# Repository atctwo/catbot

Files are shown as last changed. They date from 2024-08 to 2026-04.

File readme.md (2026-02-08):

# Cat Bot / Scratch
This repo contains the design files for **Cat Bot**, aka **Scratch**.  This is a 450g / 1lb class battlebot I made that looks like a cat.  It was designed for the [Robotics Society](https://linktr.ee/qub_robotics) at Queen's University Belfast (QRS), for competition at my local battlebots group [Combat Robotics NI](https://www.combatroboticsni.com/).

<center>
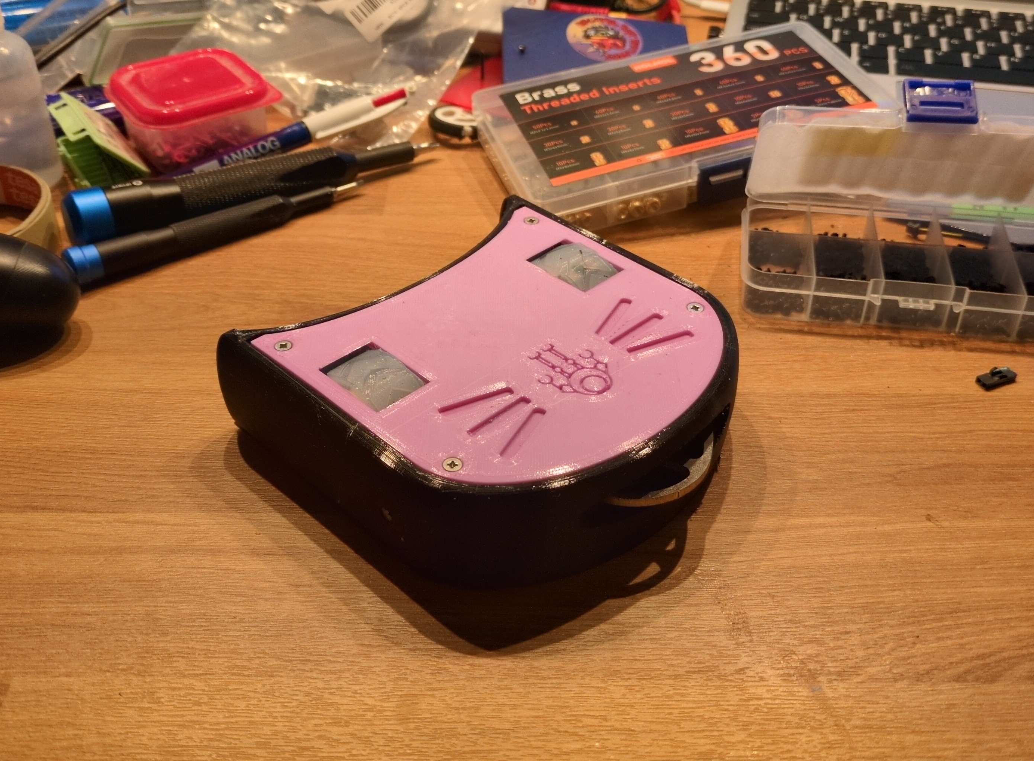
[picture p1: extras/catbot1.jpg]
A picture of Cat Bot sitting on a very messy wooden desk

</center>

# Features
- it looks like a cat :3
- (almost) the entire bot is printed from TPU to protect from impacts
- driven by two wheels (enclosed within the chassis for protection), which stick out the top and bottom to allow for operation when flipped
  - the QRS logo on the lids indicate the direction of "forward" for the motors, depending on which side is up
- multiple methods of offence
  - the cat's head is actually a plough which you can use to push opponents out of the arena
  - the cat's tongue is actually a spinner weapon so you can lick other opponents
  - you can decide which would be more useful based on your opponent
- internal walls to protect components from the wheels and the very fast spinner weapon
- designed using OpenSCAD, so *almost everything* is parametric and can be modified
- a [bill of materials](./docs/bom.md) and [build instructions](./docs/building.md) are provided to make replicating the bot easier
- external-facing screws are countersunk because it looks cool
- around 405 grams, and less than 140mm x 140mm x 40mm

# Building
A guide for building your own kitty friend are provided in [`docs/building.md`](./docs/building.md), along with the [bill of materials](./docs/bom.md)!

# Configurations
This bot was originally designed with two configurations: Little Cat and Big Cat.  As time went on, I only focused development on Little Cat so Big Cat kinda got left behind.  As such, it is deprecated and untested.  If you want to try Big Cat, check out git tag `v1.0.3`!

# Repo Structure
- [`exploded_view/`](./exploded_view/) - location to store images and render videos of an exploded view animation
- [`imports/`](./imports/) - external files imported by `cat_bot.scad` (eg: an SVG of the QRS logo)
- [`MCAD/`](./MCAD/) - submodule to [MCAD](https://github.com/openscad/MCAD), an OpenSCAD library dependency
- [`renders/`](./renders/) - exported STL versions of each part of each version of each configuration
- [`docs/`](./docs/) - documentation for the bot
  - [`building.md`](./docs/building.md) - cat bot build guide
  - [`bom.md`](./docs/bom.md) - bill of materials for each config
- [`src/`](./src/) - directory containing the OpenSCAD source code
  - [`cat_bot.scad`](./src/cat_bot.scad) - the main OpenSCAD source code file
  - [`cat_led_shim.scad`](./src/cat_led_shim.scad) - source code for the little shim that holds the power LED into the chassis
  - [`cat_wheel.scad`](./src/cat_wheel.scad) - source code for the custom wheels the bot uses
  - [`micro_metal_bracket.scad`](./src/micro_metal_bracket.scad) - a little bracket for the micro metal motors used by Little Cat
- [`readme.md`](./readme.md) - this readme!

# License
This is licensed under the MIT License - check out [`LICENSE`](./LICENSE) for more info.

# Acknowledgements
This has been one of the most interesting projects I've ever done.  I want to thank some of the people who helped me along the way!
- [Combat Robotics NI](https://www.combatroboticsni.com/) for providing a local space for destructive antweight battlebots, as well as the endless advice and assistance they've given me!
- [Team Penny](https://www.facebook.com/twopennymilk/) for their endless expertise and advice!

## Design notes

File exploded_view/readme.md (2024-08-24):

# Exploded View
This directory contains stuff to make an animated exploded view of the cat bot!

First, open `cat_bot.scad`.  Go to View -> Animate; this should open the animation bar below the 3D render pane.  Next, provide value for the FPS and Steps fields; normally I use 60 FPS and 240 steps.  Once you set these parameters the animation will start, and it will re-render the model for each step, so it can get quite laggy.  Once it's started, check the Dump Pictures box.  This will take a screenshot of each frame, and dump into the root of this repository's directory.  

After a few animation cycles and all the frames have been dumped, the Dump Pictures checkbox will uncheck itself.  Set the FPS to 0 and copy all the frame0000.png files into this directory.  To reset the model to it's unexploded state, reset the Time field to 0, then hide the animation bar.

> [!NOTE] Looping the animation
> The animation code is designed to make the animation loop automatically.  To achieve this, the model is at it's most exploded at time `$t=0.5`, and is not exploded at all at `$t=0` *and* `$t=1.0`.

Next, run [`make_exploded_view.sh`](./make_exploded_view.sh).  This will call `ffmpeg` and compile all the screenshots (specifically all .png files) into one mp4 file.  The rendered video is output as [`exploded_view.mp4`](./exploded_view.mp4):

<video controls src="exploded_view.mp4" title="Exploded View of Little Cat" loop></video>

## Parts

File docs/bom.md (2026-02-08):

# Bill Of Materials
This page lists all the parts needed to build a Cat Bot.  This is a list of all the stuff I used to build it, but a lot of it could easily be swapped out with other similar parts.  If you're using parts with different dimensions, it might be necessary to modify cat_bot.scad before printing.

Items in *italics* are need to be 3D printed.  Please refer to the [build guide](./building.md) for more detail on how to print the 3D printed parts.

| Item | Qty | Description and Notes | STL render |
|---|-----|---|---|
| **Main Chassis** | | | |
| *Chassis* | 1 | Ideally printed in TPU | [v1.3.2](../renders/little_cat/v1.3.2/main_chassis_v1.3.2a.stl) |
| *Top Lid (top)* | 1 | Ideally TPU, but PLA would probably work | [v1.3.2](../renders/little_cat/v1.3.2/top_lid_top_v1.3.2a.stl) |
| *Top Lid (bottom)* | 1 | Printed with PLA | [v1.3.2](../renders/little_cat/v1.3.2/top_lid_bottom_v1.3.2a.stl) |
| *Bottom Lid* | 1 | Ideally TPU, but PLA would probably work | [v1.3.2](../renders/little_cat/v1.3.2/bottom_lid_v1.3.2a.stl) |
| **Motors and Wheels** | | | |
| Micro Metal (N20) Gearbox Motor | 2 | 298:1 ratio is recommended | |
| *Micro Metal Bracket* | 2 | Printed with PLA or PETG | [v2](../renders/wheels/micro_metal_bracket_v2.stl) |
| Micro Metal Shim | 2 | Little shims made by [Pimoroni](https://shop.pimoroni.com/products/motor-shim-pack-of-5?variant=24169581255) so you don't have to solder directly to the motors | |
| Wheels | 2 | The bot is designed to use any 42mm diameter, 3mm shaft wheels.  However, this cat has custom wheels if you want to make them! |
| <em>&nbsp;&nbsp;&nbsp;&nbsp;Cat Wheel Hub</em> | 2 | Main hub of the wheels, printed in TPU | [v3](../renders/wheels/cat_wheel_v3.0_hub.stl) |
| <em>&nbsp;&nbsp;&nbsp;&nbsp;Cat Wheel Axel Insert</em> | 2 | 3mm shaft compatible insert, inserted into hub ([source](cat_wheel.scad), [STL](./renders/wheels/cat_wheel_v2_insert.stl)) | [v3](../renders/wheels/cat_wheel_v3.0_insert.stl) |
| <em>&nbsp;&nbsp;&nbsp;&nbsp;Cat Wheel Tyre</eM> | | Tyres for the wheels, cast out of silicone (again, pls refer to the build guide for more info!) | [v3](../renders/wheels/cat_wheel_v3.0_tyre.stl) |
| **Weapon** | | | |
| 60mm spinning blade | 1 | Currently using [this one](https://www.ull-robotics.com/shop/p/60mm-dia-disc) from ULL Robotics<br>Previously used [this one](https://monsoonrobotics.co.uk/collections/bars-and-discs) from Monsoon Robotics| |
| Brushless Motor | 1 | I'm currently using a BE1806 ([eg: this one from Bristol Bot Builders](https://shop.bristolbotbuilders.com/product/brushlessmotor/))| |
| **Electronics** | | | |
| Electronic Speed Controller | 1 | I used [this dual ESC](https://shop.bristolbotbuilders.com/product/bbbv3/) from BBB to drive both wheels | |
| ESC for the weapon | 1 | Currently using a [Favorite Little Bee Spring 20A](https://www.ull-robotics.com/shop/p/m89iboau1osvfcs04i9ip4hepujcb5)<br>Previously used [this weapon ESC](https://shop.bristolbotbuilders.com/product/brushless/) from BBB | |
| Receiver | 1 | Often RC receivers are used like [this one from BBB](https://shop.bristolbotbuilders.com/product/flysky/) (but my cat uses an [ESP32](https://www.adafruit.com/product/5395) and [some funky Bluetooth controller firmware I made](https://github.com/atctwo/bbrx)) | |
| Power switch | 1 | The one cat bot is designed for is [this one from BBB](https://shop.bristolbotbuilders.com/product/switch/) | |
| Battery | 1 | I used a 300 mAh LiPo because its what I had on hand, but keep in mind: <ul><li>make sure yours will fit in the chassis</li><li>make sure it can source enough current to power all the motors</li></ul> | |
| Battery connectors | 2P  | Need at least one for the battery.  I have one on both sides of the power switch so I can remove the switch assembly from the rest of the bot.  The type and gender of connectors you need will depend on what connector your battery has |
| Power LED | 1 | Any old 5mm LED and a current limiting resistor (although my builds use a [5mm WS2812B](https://www.sparkfun.com/led-rgb-addressable-pth-5mm-clear-5-pack.html) so the ESP32 can use it as a status LED too) |
| *Power LED shim* | 1 | A little thingy to hold the LED into a hole in the chassis.  Printed in transparent PLA | [v1](../renders/cat_led_shim.stl) |
| **Screws** | | | |
| M3x7 (pan) | 8 | Mounting screws motor brackets | |
| M3x10 (countersunk) | 8 | Mounting screws for lids; at least 10mm long | |
| M2x6 (countersunk) | 4 | Mounting screws for the weapon motor | |
| M2x8 (countersunk) | 2 | Fixing the edge of the bottom lid to the chassis | |
| M2x6 (pan) | 4 | Screws to mount the weapon onto the motor (use wider / thicker heads to avoid the force of the weapon bending them)  | |
| M2.5x4 | 2 | Mounting the power switch to the chassis | |
| **Inserts** | | | |
| M3x4 | 8 | Mounts for motor brackets | |
| M3x4 again | 8 | Mounts for lid | |
| M2x3 | 2 | Extra support mounts for the bottom lid around the motor | |
| M2.5x3 | 2 | Mounts for the power switch | |

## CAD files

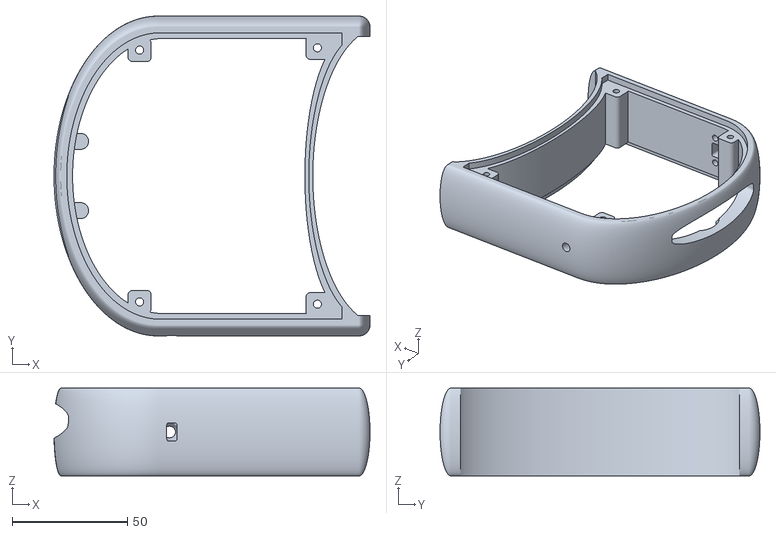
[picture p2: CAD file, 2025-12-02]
renders/little_cat/v1.3.2/main_chassis_v1.3.2a.stl
136.8 x 138.5 x 38.0

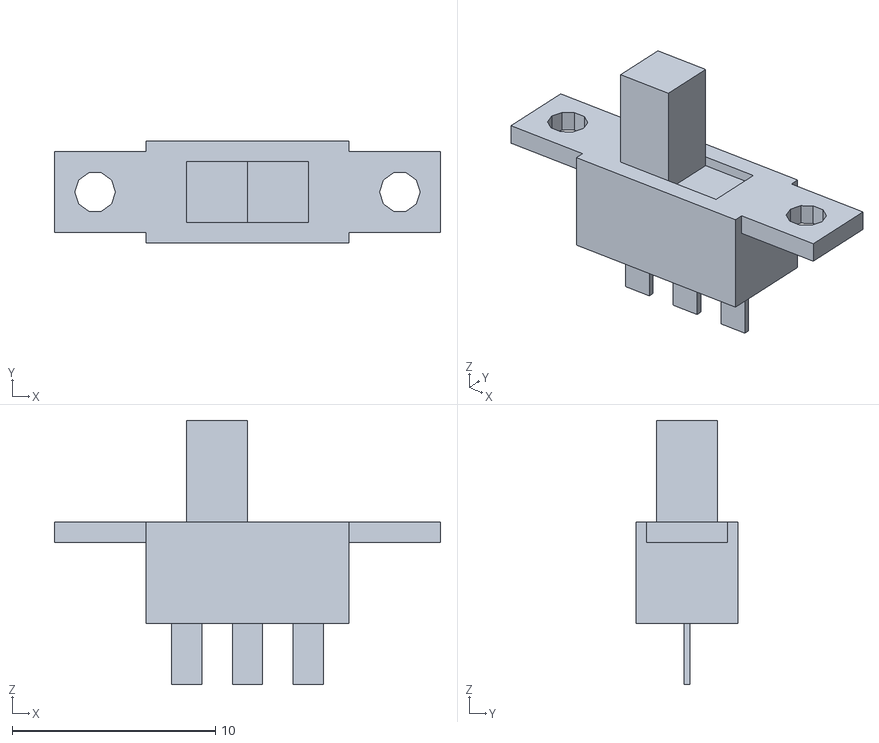
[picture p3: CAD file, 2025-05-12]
imports/switch.stl
19.0 x 5.00 x 13.0

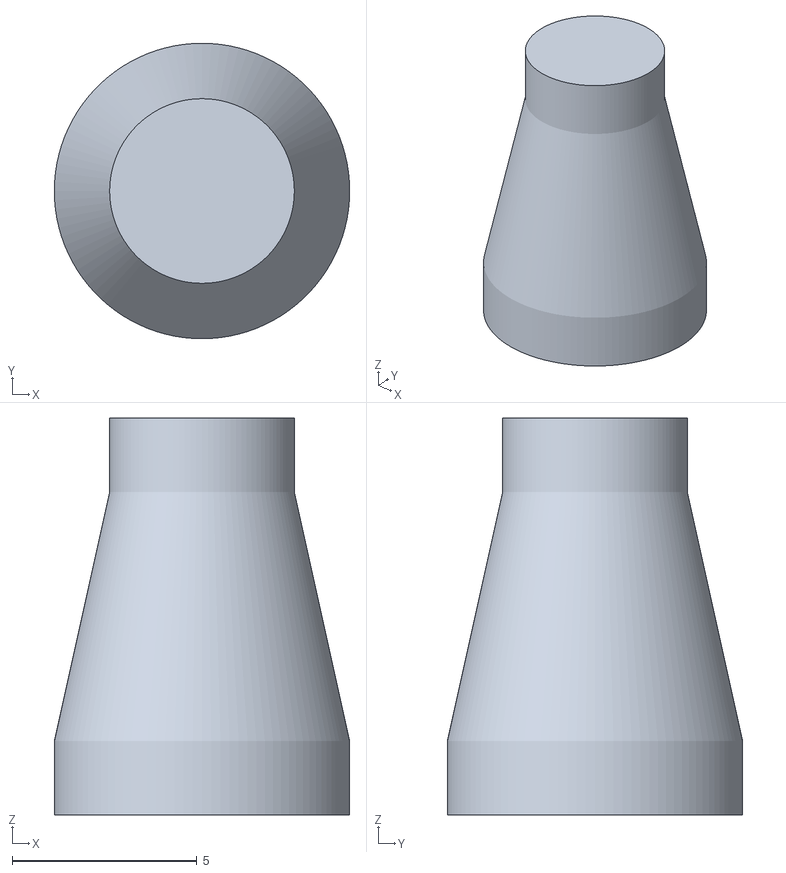
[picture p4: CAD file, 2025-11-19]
renders/cat_led_shim.stl
8.00 x 8.00 x 10.8

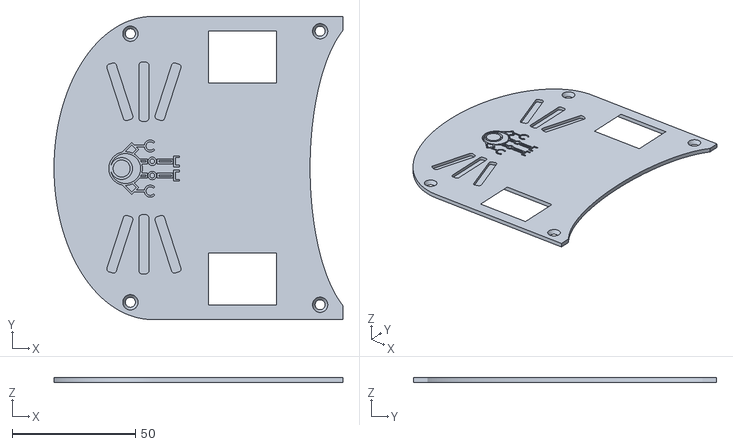
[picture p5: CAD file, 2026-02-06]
renders/little_cat/v1.3.2/top_lid_top_v1.3.2a.stl
117.3 x 123.0 x 2.00

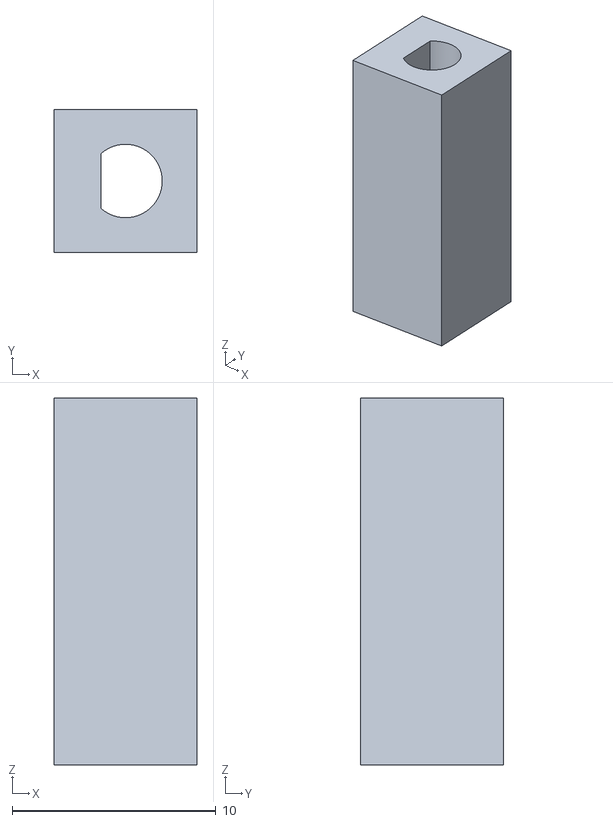
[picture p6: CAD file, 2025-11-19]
renders/wheels/cat_wheel_v3.0_insert.stl
7.00 x 7.00 x 18.0

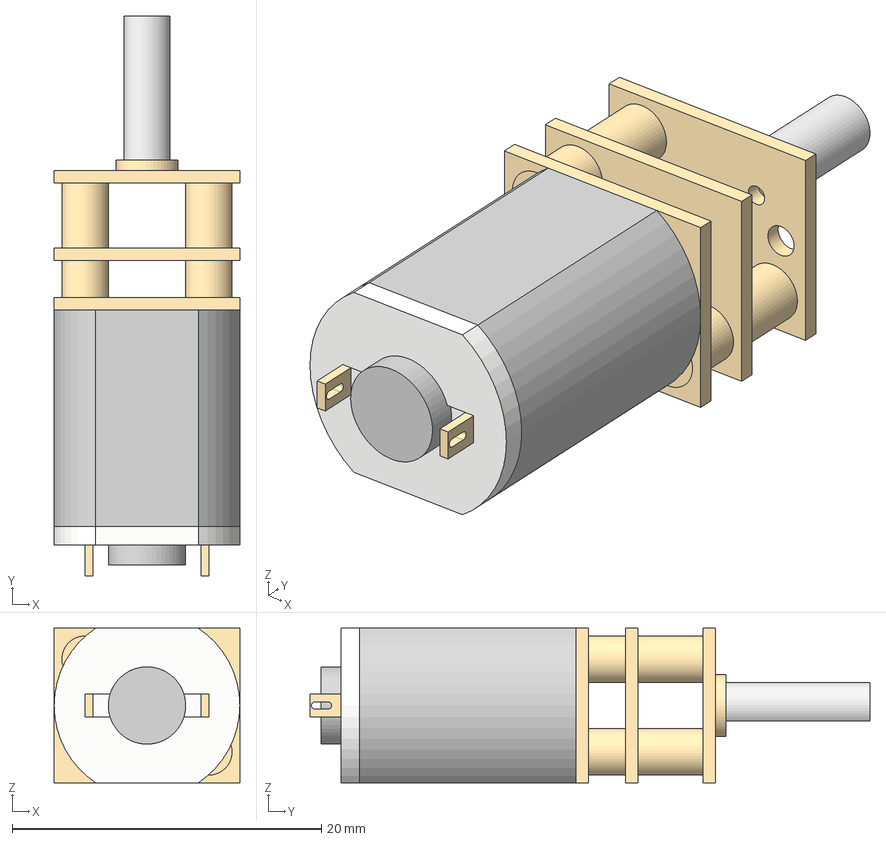
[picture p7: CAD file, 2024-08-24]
imports/N20 v2.step
12.0 x 36.2 x 10.0 mm

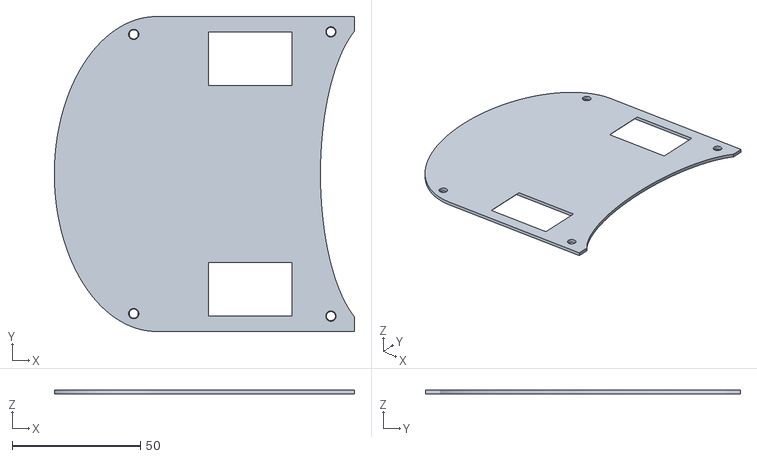
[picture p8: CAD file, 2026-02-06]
renders/little_cat/v1.3.2/top_lid_bottom_v1.3.2a.stl
117.3 x 123.0 x 1.50

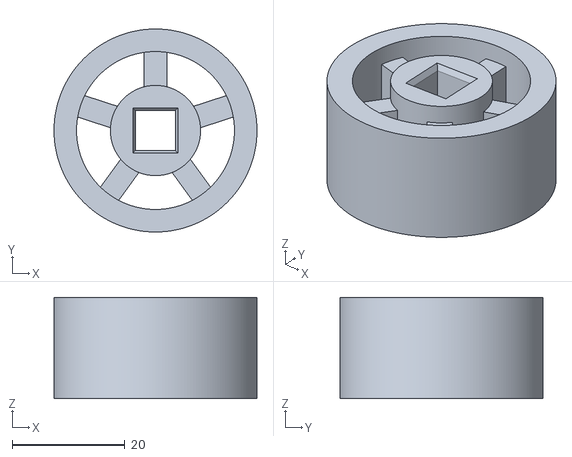
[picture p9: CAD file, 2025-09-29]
renders/wheels/cat_wheel_v2_hub_36mm.stl
36.0 x 36.0 x 18.0

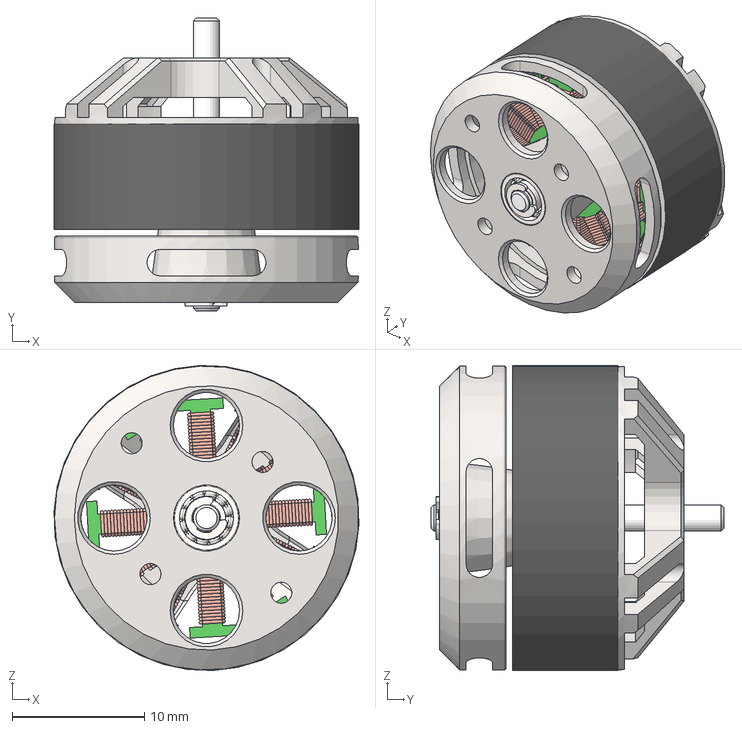
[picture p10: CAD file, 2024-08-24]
imports/1806.step
23.1 x 22.2 x 23.1 mm

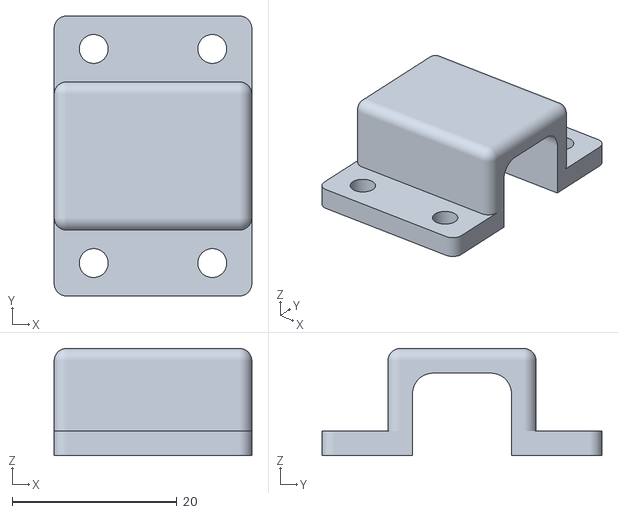
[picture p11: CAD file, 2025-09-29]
renders/wheels/micro_metal_bracket_v2.stl
24.0 x 34.0 x 13.0

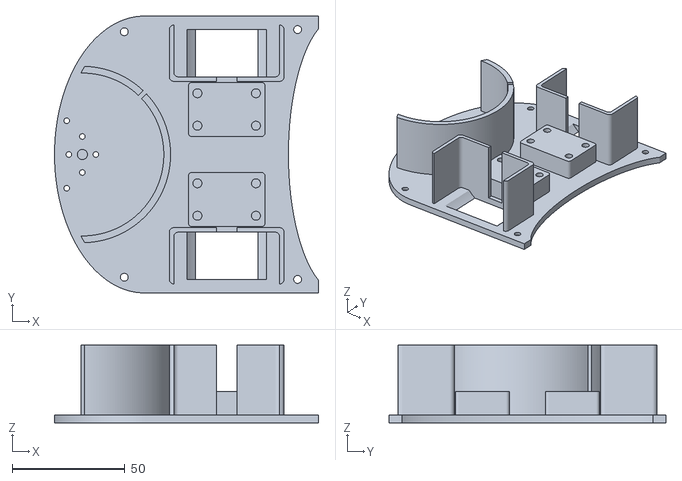
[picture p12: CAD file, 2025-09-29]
renders/little_cat/v1.3.2/bottom_lid_v1.3.2a.stl
117.3 x 123.0 x 34.5

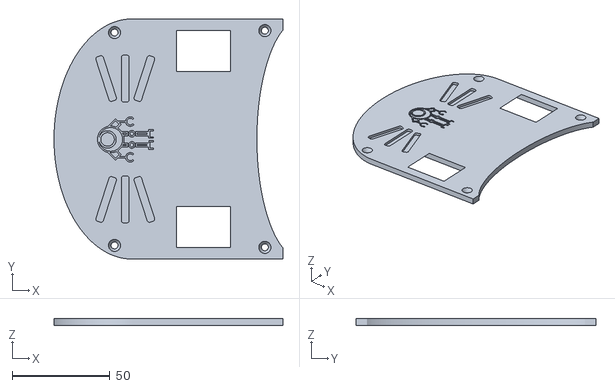
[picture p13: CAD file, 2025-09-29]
renders/little_cat/v1.3.2/top_lid_v1.3.2a.stl
117.3 x 123.0 x 3.50

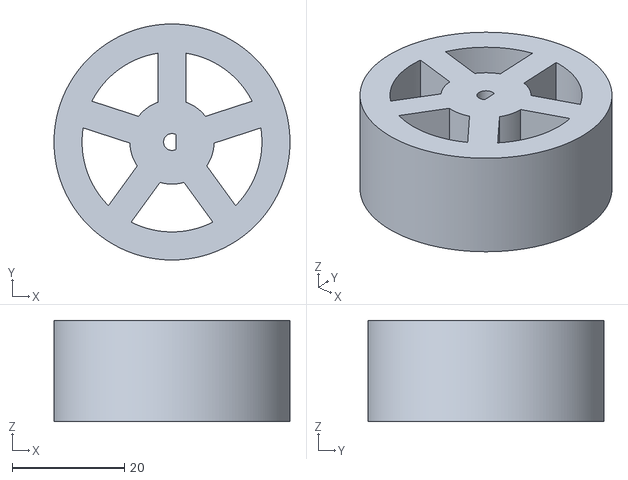
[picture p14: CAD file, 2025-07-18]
renders/wheels/cat_wheel_42mm.stl
42.0 x 42.0 x 18.0

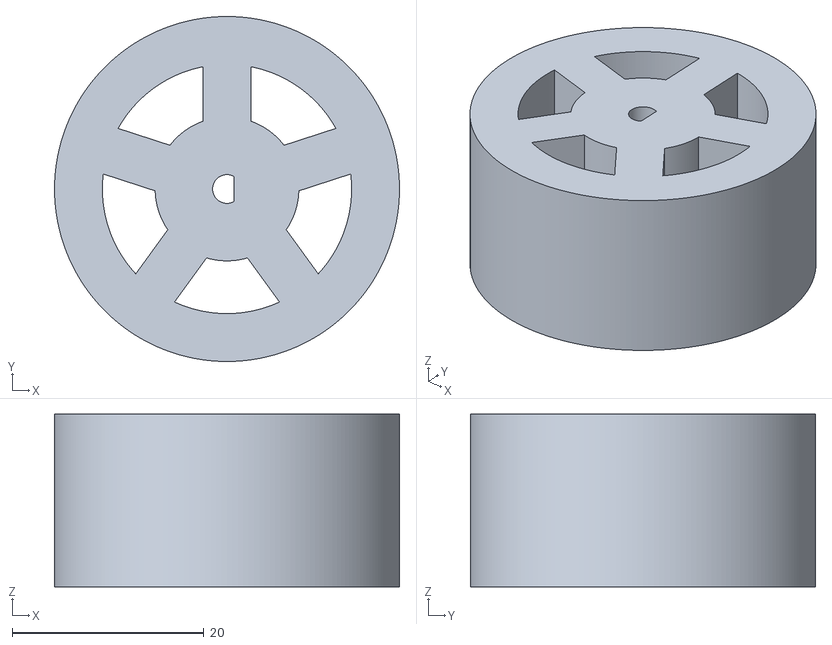
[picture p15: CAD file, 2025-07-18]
renders/wheels/cat_wheel_36mm.stl
36.0 x 36.0 x 18.0

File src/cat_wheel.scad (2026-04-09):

/*
 * Cat Bot Wheels v4.0
 * made by alex (atctwo) in july - apr 2026
 * no idea how well these will work so i guess we'll see!
 * please print in something squishy and grippy (eg: TPU)
 *
 */

wheel_d = 42;                       // overall wheel diameter, including all parts
wheel_h = 18;                       // wheel height (tread thicknes)
hub_ot = 4;                         // thickness of the outer section of the hub
hub_id = 16;                        // diameter of the inner hub
hub_m = 0.1;                        // space between the hub and the tyre
tyre_t = 4;                         // thickness of the outer tyre

guard_t = 2;                        // thickness of the guard on both sides of the wheel
guard_d = 40;                       // diameter of the guards

n_spokes = 5;                       // number of spokes
spoke_t = 4;                        // thickness of each spoke
spoke_h = 12;                       // height of each spoke
shaft_d = 3.6;                      // shaft diameter
shaft_flat_offset = 2.5/3;          // how much of the shaft should be curved (ie: inverse of how much should be taken up by the flat edge)

split_hub = true;                   // whether to split the hub into a separate square bit
split_hub_size = [7, 7];            // size of the split hub
split_hub_padding = 0.01;           // how much bigger to make the hub hole in the wheel

split_hub_chamfer_angle = 45;
split_hub_chamfer_height = 1;

tooth_h = 12;                       // height of teeth (perpendicular to height of the wheel)
tooth_w = 2;                        // width of the teeth (ie: how much do they extend from the hub)
// tooth_a = 360 * ((-(2*$t) ^ 2) + (4*$t));
tooth_a = 20;                       // tooth arc (ie: how much of a circle sweep does each tooth make)
n_teeth = 5;                        // number of teeth
tooth_thingy_h = 10;              // height of the crescent shape removed from the teeth
tooth_thingy_w = 1.5;               // width of the crescent shape removed from the teeth

chevron_w = 4;                      // width of each chevron trench
chevron_d = 1.5;                      // depth of each chevron trench
chevron_a = 120;                    // angle the two parts of each chevron are to each other
n_chevron = 12;                     // number of chevrons across surface of wheel

tyre_edge_trim_h = 1;               // height of the bit around the tyre edges to remove
tyre_edge_trim_d = chevron_d;       // depth of the bit around the tyre edges to remove

raw_wheel_h = wheel_h - (guard_t * 2);
hub_d = wheel_d - (hub_m*2) - (tyre_t*2);     // outer diameter of the inner hub
tooth_dz = (raw_wheel_h - tooth_h) / 2;
tooth_thingy_dx = (tooth_w) / 2;
tooth_thingy_dh = (tooth_h - tooth_thingy_h) / 2;

show_tyre = true;                   // whether to show the outer tyre
show_wheel = true;                  // whether to show the inner hub
show_split_hub = true;              // whether to show the axel insert

enable_hub_teeth = true;            // whether to enable teeth on the hub
enable_tyre_teeth = true;           // whether to enable negative teeth in the tyres
enable_chevrons = true;             // whether to show chevrons on the tyres
enable_guards = true;               // whether to enable tyre guards on both sides of the wheel

$fn = 200;

// main wheel
if (show_wheel)
translate([0, 0, guard_t])
// color("#222222") {
color("#00ced1") {
    difference() {

        union() {
        // outer bit
        difference() {
            
            // outer cylinder
            cylinder(d=hub_d, h=raw_wheel_h);

            // inner hollow
            translate([0, 0, -0.5])
            cylinder(d=hub_d-(hub_ot*2), h=raw_wheel_h+1);
        }

        // spokes
        for (i=[0:n_spokes]) {
            rotate([0, 0, i*(360/n_spokes)])
            translate([-spoke_t/2, 0, (raw_wheel_h-spoke_h)/2])
            cube([spoke_t, (hub_d/2)-(hub_ot/2), spoke_h]);
        }

        // inner bit
        difference() {
            cylinder(d=hub_id, h=raw_wheel_h);
        }

        // teeth
        if (enable_hub_teeth)
        for (i=[0:n_teeth]) {
            rotate([0, 0, i*(360/n_teeth)])
            cresent_tooth();
        }

    }

        // d-shaft
        if (!split_hub) d_shaft();
        else {
            split_hub_hub(split_hub_padding, 1);
            
            // chamfer on bottom
            translate([0, 0, split_hub_chamfer_height])
            rotate([180, 0, 0]) 
            split_hub_chamfer(split_hub_padding);
            
            // chamfer on top
            translate([0, 0, raw_wheel_h-split_hub_chamfer_height])
            rotate([0, 0, 0]) 
            split_hub_chamfer(split_hub_padding);
        }
    }
}


// split hub
if (show_split_hub)
translate([0, 0, guard_t])
if (split_hub) {
    difference() {
        split_hub_hub();
        d_shaft();
    }
}



// tyres
if (show_tyre)
translate([0, 0, guard_t]) {
    
    translate([0, 0, 0.0005])
    color("#ffeeee", 0.9)
    difference() {
        
        // outer diameter
        cylinder(d=wheel_d, h=raw_wheel_h-0.001);

        // hole for the hub to go in
        translate([0, 0, -0.5])
        cylinder(d=(wheel_d-(tyre_t*2))-(hub_m*2), h=raw_wheel_h+1);

        // negative teeth
        if (enable_tyre_teeth)
        render() {
            for (i=[0:n_teeth]) {
                rotate([0, 0, i*(360/n_teeth)])
                cresent_tooth();
            }
        }

        // chevrons
        if (enable_chevrons) {
            render() {
                chevrons();
            }
        }

        // edge trim
        difference() {
            union() {
                cylinder(d=wheel_d, h=tyre_edge_trim_h);
                translate([0, 0, raw_wheel_h-tyre_edge_trim_h])
                cylinder(d=wheel_d, h=tyre_edge_trim_h);
            }
            translate([0, 0, -0.5])
            cylinder(d=wheel_d-tyre_edge_trim_d, h=wheel_d+1);
        }
    }
}

// tyre guards
color("gray")
if (show_wheel)
if (enable_guards) {
    difference() {
        union() {
            cylinder(d=guard_d, h=guard_t);
            translate([0, 0, raw_wheel_h+guard_t])
            cylinder(d=guard_d, h=guard_t);
        }
        translate([0, 0, -0.5])
        cylinder(d=hub_d-(hub_ot*2), h=wheel_h+1);
    }
}



module split_hub_hub(padding=0, ph=0) {
    translate([0, 0, (raw_wheel_h/2)])
    cube([split_hub_size.x+padding*2, split_hub_size.y+padding*2, raw_wheel_h+ph], center=true);
}

module split_hub_chamfer(padding=0) {
    chamfer_size = [
        (split_hub_size.x + padding*2) + tan(split_hub_chamfer_angle) * split_hub_chamfer_height,
        (split_hub_size.y + padding*2) + tan(split_hub_chamfer_angle) * split_hub_chamfer_height
    ];

    chamfer_shape(
        (split_hub_size.x+padding*2) / 2, (split_hub_size.y+padding*2) / 2,
        chamfer_size.x / 2, chamfer_size.y / 2, 
        split_hub_chamfer_height
    );
    
}
    
module d_shaft() {
    translate([0, 0, -0.5])
    difference() {
        cylinder(d = shaft_d, h=raw_wheel_h+1);
        translate([-split_hub_size.x/2, -split_hub_size.y/2, 0])
        cube([((split_hub_size.x-shaft_d)/2)+(shaft_d*(1-shaft_flat_offset)), split_hub_size.x, raw_wheel_h+1]);
    }
}

module chamfer_shape(w1, l1, w2, l2, h) {
    polyhedron(
      points=[ 
        [w1,l1,0],[w1,-l1,0],[-w1,-l1,0],[-w1,l1,0], // the four points at base
        [w2,l2,h],[w2,-l2,h],[-w2,-l2,h],[-w2,l2,h]
      ],
      faces = [
        [0,1,2,3],
        [7,4,0,3], [6,7,3,2], [5,6,2,1], [4,5,1,0],
        [4,5,6,7]
      ]);                   // two triangles for square base
    
}

// need to make it smaller at top
// maybe have w_bottom, l_bottom, w_top, l_top
//!chamfer_shape(10, 10, 5, 5, 10);





// sector
// from https://openhome.cc/eGossip/OpenSCAD/SectorArc.html
module sector(radius, angles, fn = 24) {
    r = radius / cos(180 / fn);
    step = -360 / fn;

    points = concat([[0, 0]],
        [for(a = [angles[0] : step : angles[1] - 360]) 
            [r * cos(a), r * sin(a)]
        ],
        [[r * cos(angles[1]), r * sin(angles[1])]]
    );

    difference() {
        circle(radius, $fn = fn);
        polygon(points);
    }
}

module cresent_tooth() {
    rotate([0, 0, 90+(tooth_a/2)])
    translate([0, 0, tooth_dz])
    difference() {

        // extrude into circle
        translate([0, 0, tooth_h/2])
        rotate_extrude(convexity=10) {
            translate([hub_d/2, (-tooth_h/2)+(tooth_w), 0])

            // tube thing base
            difference() {

                // main tube
                hull() {
                    circle(d=tooth_w*2);

                    translate([0, tooth_h-(tooth_w*2), 0])
                    circle(d=tooth_w*2);
                }

                // remove inner part
                translate([-tooth_w-1, -tooth_w, 0])
                square([tooth_w+1, tooth_h]);
            }
        }
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

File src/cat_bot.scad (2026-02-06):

/*
 *  Queen's Robotics Society
 *  Antweight Battlebot
 *
 *  Designed in 2024 - 2025 by
 *  - alex barnes (@atctwo)
 *
 *  This bot looks like the following things:
 *  - a cat
 *  - the data storage symbol in flowchart-based software design
 *  - a logical OR gate (or NOR if you consider the spinner an inversion circle)
 */

use <../MCAD/boxes.scad>
use <micro_metal_bracket.scad>
use <cat_led_shim.scad>

///////////////////////////////////////////
//
//    Parameters
//
///////////////////////////////////////////

/* [Base Dimensions] */

// base width of the whole bot
base_w_raw = 135;

// base length of the whole bot
base_d_raw = 135;

// base height of the whole bot chassis
base_h = 38;

/* [Plough Dimensions] */

// width of the plough
plough_w = 30;

// length of the plough
plough_d = base_d_raw;

// height of the plough
plough_h = base_h;

// offset of the curve which makes the plough
plough_offset = [10, 0, 0];

// rotation of the plough
plough_rotation = [0, 0, 0];

/* [Weapon Section of Chassis] */

// width of the curved bit which holds the weapon
weapon_w = 42;

// length of the curved bit
weapon_d = base_d_raw;

// height of the weapon
weapon_h = base_h;

/* [Weapon Size and Position] */

// diameter of the spinner
weapon_diameter = 60.33;

// thickness of the spinner
weapon_thickness = 3;

// extra diameter to add to the spinner to make the hole wider
weapon_diameter_padding = 10;

// extra thickness to add to the spinner to make the hole taller
weapon_thickness_padding = 10;

// height from the top of the bottom lid that the spinner sits (ie: motor height)
weapon_z = 18.5;

// diameter of the spinner motor
weapon_motor_diameter = 23;

// if the motor eats into the main chassis, pad it by this much
weapon_motor_padding = 3;

// extra offset for the motor and spinner
weapon_offset = [15.4, 0, 0];

// diameter of weapon screw holes (main body)
weapon_mount_screw_cd1 = 2.5;

// diameter of weapon screw holes (countersink)
weapon_mount_screw_cd2 = 3.8;

// size of the countersunk head of weapon screw holes
weapon_mount_screw_ch = 2;

// positions of the screws holes for the weapon (expressed as distances from the motor axle)
weapon_mount_screws = [
    [0,-8], [0,8],
    [-6,0], [6,0]
];

// do you want a big hole where the axle sticks out the bottom of the motor?
weapon_axle_hole_d = 4.5;

// how deep do you want that hole to be?  as a percent of the lid thickness
weapon_axle_hole_h = 0.5;

// thickness of the protective walls around the spinner
weapon_wall_thickness = 3;

// gap between the spinner area and the protective walls (note: other interior stuff has a separate variable, interior_wall_gap)
weapon_wall_gap = 2;

/* [Chassis Features] */

// whether to make a big hole for the spinner to extend out of
chassis_show_weapon_hole = true;

// whether to make the sides of the chassis curved
chasss_curved_walls = true;

/* [Interior and Lid Dimensions] */

// thickness of the shell's walls
interior_wall_thickness = 2.5;

// thickness of the lids
interior_lid_thickness = 3.5;

// gap between outer edge of lids and inner edge of interior
interior_lid_gap = 0.5;

// use this param to split the lid into two halves - this is the height of the top half
interior_lid_split = 2;

// how thick the interior shelf should be
interior_shelf_thickness = 2.5;

// width of the lid mounting posts
interior_lid_mounting_w = 10;

// length of the lid mounting posts
interior_lid_mounting_d = 10;

// radius of the lid mounting posts
interior_lid_mounting_r = 2;

// diameter of the mounting hole
interior_lid_mounting_hole_d = 3.5;  // M3 brass insert

// screw diameters have 0.5mm added for normal padding, and an extra 0.4mm for my shrinky filament

// screw hole diameter
interior_lid_mounting_hole_cd1 = 3.5;

// screw hole countersink diameter
interior_lid_mounting_hole_cd2 = 6.2;

// height of the screw head
interior_lid_mounting_hole_ch = 2.5;

// min gap between interior features and the shelf (note: weapon has a separate variable, weapon_wall_gap)
interior_wall_gap = 4.0;

/* [Lid Mounting Hole Positions] */

// how far along the x axis the top left post is
lid_mh_tlw = 0.8; // .1

// how far along the x axis the bottom left post is
lid_mh_blw = 1.8; // .1

// how far along the x axis the top right post is
lid_mh_trw = 0.8; // .1

// how far along the x axis the bottom right post is
lid_mh_brw = 1.8; // .1

// how far along the y axis the top left post is
lid_mh_tld = 1.0; // .1

// how far along the y axis the top right post is
lid_mh_trd = 1.0; // .1

// how far along the y axis the top left post is
lid_mh_bld = 0.9; // .1

// how far along the y axis the top right post is
lid_mh_brd = 0.9; // .1

/* [Interior and Lid Features] */

// which gearbox / motors to enable
interior_gearbox = "micro"; // [none:None, double:Tamiya Double Gearbox, micro:Micro Metal Gearboxes]

// whether to make holes for the screws to attach the lid to the chassis
interior_show_screw_holes = true;

// whether to make holes in the lid for wheels
interior_show_wheels = true;

// whether to show walls around the wheel areas
interior_show_wheel_walls = true;

// whether to create any mounting stuff for the selected gearbox
interior_show_gearbox_mounting = true;

// whether to create walls around the spinner area
interior_show_weapon_walls = true;

// whether to have a wee hole for the wires to go out of
interior_weapon_wall_hole = true;

// diameter of the hole
interior_weapon_wall_hole_d = 6;

// angle along the weapon wall to have the hole
interior_weapon_wall_hole_a = 45;

// width of the hole to make for the wires
interior_weapon_wall_slot_w = 2;

// whether to show weapon stabiliser mounts
interior_show_weapon_stabilisers = true;

// diameter of the weapon stabiliser mounts (should be greater than weapon_stabiliser_insert_d by at least a bit)
weapon_stabiliser_mount_d = 7;

// height of the weapon stabiliser mounts (should be greater than weapon_stabiliser_insert_h by at least a bit)
weapon_stabiliser_mount_h = 6;

// position of the brass insert mounts for the weapon stabilisers; make sure the generated posts are physically connected to the main chassis
weapon_stabiliser_mount_offset = [-7, 15];

// the weapon stabiliser mounts are actually made by taking the hull of two cylinders.  if one of the cylinders is placed inside the chassis walls, then the overall shape has a stronger connection to the chassis.  use this offset to determine the position of the "joining" cylinder
weapon_stabiliser_mount_hull_offset = [-3, 0];

// diameter of the brass insert holes for the weapon stabilisers
weapon_stabiliser_insert_d = 3;

// depth of the brass insert holes for the weapon stabilisers
weapon_stabiliser_insert_h = 5;

// smaller diameter for the weapon stabiliser mounting holes on the bottom lid
weapon_stabiliser_screw_d1 = 2.5;

// larger (countersink) diameter for the weapon stabiliser mounting holes on the bottom lid
weapon_stabiliser_screw_d2 = 3.8;

// height of the countersunk head for the weapon stabiliser mounting holes on the bottom lid
weapon_stabiliser_screw_ch = 2;

// padding to add to things on the interior that go up against the inner shelf
interior_padding_against_shelf = 1;

// power switch position x coord
interior_power_switch_x = 48;

// power switch position z offset (by default it's in the middle)
interior_power_switch_z_offset = 0;

// size of the hole to make for the power switch
interior_power_switch_hole = [8, 4.5];

// diameter of the holes to make for the switch mounts
interior_power_switch_mount_d = 3.5;

// depth of the holes to make for the switch mounts
interior_power_switch_mount_h = 4;

// how far along the x-axis the led hole should be
led_shim_x_offset = 47;

/* [Wheels and Gearbox Size and Position] */

// thickness / tread size of the wheels
wheel_tread = 18; // .1

// padding to add to the wheel holes for the tread
wheel_tread_padding = 3; // .1

// diameter of the wheels
wheel_diameter = 42; // .1

// extra diameter to add to the wheels to make the holes bigger
wheel_diameter_padding = 5; // .1

// distance of the centres of the two wheels from the centre of the robot
wheel_separation = 90; // .1

// vector by which to offset the wheels from the centre of the bot
wheel_offset = [15, 0, 0]; //.1

// diameter of the gearbox axel
wheel_axel_d = 3; // .1

// thickness of the wheel walls
wheel_wall_thickness = 2; // .1

// radius of the corners on the wheel walls
wheel_wall_radius = 2; // .1

// radius of the blocks that make up the gearbox mount
gearbox_mount_radius = 2; // .1

// this can be used to move the motors closer together
bracket_y_offset = 0.5;

/* [Lid Decoration] */

// how deep the rescess of decorations are on the lids
lid_decoration_depth = 1.5;

// offset of the main decoration (qrs logo, whiskers)
lid_main_decoration_offset = [-25, 0, 0];

// whether to show the QRS logo on the lids
lid_show_qrs_logo = true;

// dpi of the QRS logo on the lids (bigger DPI -> smaller physical size)
qrs_logo_dpi = 425;
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

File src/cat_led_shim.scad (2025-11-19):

/*
 * Cat Bot LED Shim v1
 * made by alex (atctwo) in november 2025
 * 
 * this is a little dohickey to mount an LED into the side
 * of cat bot's chassis.  the idea is that the LED is held
 * in place without sticking out the side of the chassis.
 * this should be printed in some type of transparent filament
 * so that the light shines through
 *
 * Please consider printing with ??? infill and
 * a concentric top/bottom pattern to avoid interfering with
 * the light's output path
 *
 */

// diameter of the hole on the outside
do = 5;

// diameter of the hole on the inside
di = 8;

// amount by which the shim protrudes from the outside
pro = 0;

// amount by which the shim protrudes from the inside
pri = 1;

// amount by which the shim extends into the outside side
exo = 2;

// amount by which the shim extends into the inside side
exi = 1;

// diameter of the LED hole on the inside
dl = 5.1; // d=5.0±0.2mm, shelfy bit is 5.8±0.2mm

// depth of the LED hole on the inside
wl = 8.0; // 8.7±0.2mm incl shelfy bit

// led offset
ol = 3.5;

// depth of the chassis
wc = 4.75 + 2.5 + 2.5;

// resolution of curved faces
$fn = 100;


module led_hole() {
    sphere(d=dl);
    translate([0, 0, -(wl-(dl/2))])
    cylinder(d=dl, h=wl-(dl/2));
}

module cat_led_shim(show_led_hole=false) {

    difference() {
        union() {

            // base cylinder for the inside side
            translate([0, 0, -pri])
            cylinder(h=pri+exi, d=di);

            // base cylinder for the outside side
            translate([0, 0, wc-exo-(0.0001/2)])
            cylinder(h=pro+exo+0.0001, d=do);

            // da cone
            translate([0, 0, pri])
            cylinder(d1=di, d2=do, h=(wc-exo-exi));

        }

        // led hole
        if (show_led_hole) {
            translate([0, 0, ol])
            led_hole();
        }
    }

}

if (0)
difference() {
    union() {
        difference() {

            // mock chassis
            color("black")
            translate([-(di), -(di), 0])
            cube([di*2, di*2, wc]);

            // shim
            cat_led_shim();        
        }
    }
// the slicerrr
translate([-di*1.5, 0, -wc/2])
cube([di*3, di*2, wc*2]);
}

color("teal", 0.8)
cat_led_shim(true);

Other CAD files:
renders/little_cat/v1.2.0/main_chassis_v1.2.0a.stl
renders/little_cat/v1.2.1/main_chassis_v1.2.1a.stl
renders/little_cat/v1.3.0/main_chassis_v1.3.0a.stl
renders/big_cat/v1.0.1/main_chassis.stl
src/micro_metal_bracket.scad
imports/N20 v2.stl
renders/big_cat/v1.0.0/lid_bottom.stl
renders/big_cat/v1.0.1/lid_bottom.stl
renders/big_cat/v1.0.1/lid_top.stl
renders/big_cat/v1.0.1/tpu_shielding.stl
renders/little_cat/v0.1.0/lid_bottom.stl
renders/little_cat/v1.0.0/lid_bottom.stl
renders/little_cat/v1.0.0/lid_top.stl
renders/little_cat/v1.0.0/main_chassis.stl
renders/little_cat/v1.0.0/tpu_shielding.stl
renders/little_cat/v1.0.1/lid_bottom.stl
renders/little_cat/v1.0.1/lid_top.stl
renders/little_cat/v1.0.1/main_chassis.stl
renders/little_cat/v1.0.1/tpu_shielding_hole.stl
renders/little_cat/v1.0.1/tpu_shielding_no_hole.stl
renders/little_cat/v1.0.2/tpu_shielding_hole.stl
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

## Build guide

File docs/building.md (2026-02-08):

# Building Your Own Cat
So, you want to build your own Cat Bot?  This document details the entire process, from 3D printing the chassis parts, to wiring, to assembly.  I would recommend first taking a look at the [bill of materials](./bom.md) to get an idea of all the parts you'll need.  Next, read through this page to get an idea of the entire process before starting.

Most importantly, have fun and enjoy your new combat friend!

<center>
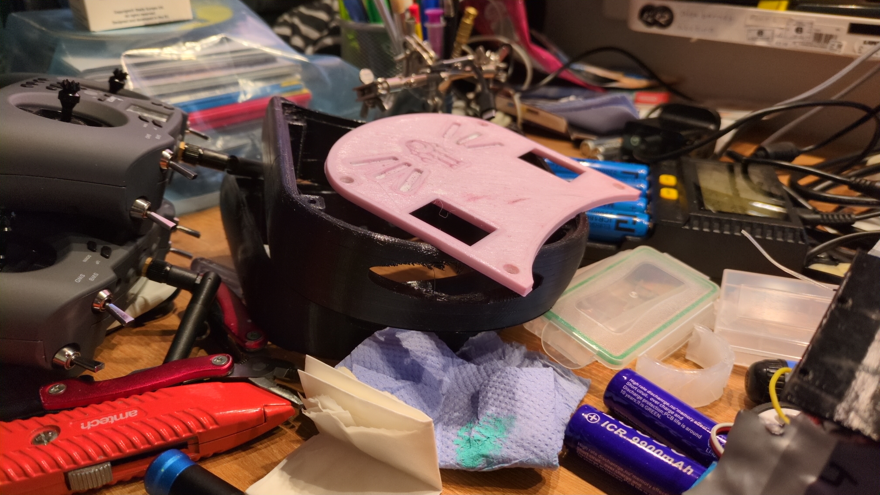
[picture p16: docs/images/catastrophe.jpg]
A pile of 3D printed cat bot parts stacked in the middle of a very messy desk

</center>

## Contents
- [Building Your Own Cat](#building-your-own-cat)
  - [Contents](#contents)
- [Gather and Make Parts](#gather-and-make-parts)
  - [Wheels](#wheels)
  - [Colours](#colours)
  - [Next Part](#next-part)
- [Wiring](#wiring)
- [Assembly](#assembly)
  - [Bottom Lid](#bottom-lid)
  - [Chassis and Weapon](#chassis-and-weapon)

# Gather and Make Parts
Most of the structural parts of the bot are designed to be 3D printed (or molded), while the rest can be purchased.  An overview can be found in the BOM, but here are the full details.

> [!NOTE]
> When printing parts for the bot, pre-rendered renders of each part are provided in the [`renders`](../renders/) directory.  But if you're making changes to the OpenSCAD source, make sure to clone this repo's submodules (specifically [MCAD](https://github.com/openscad/MCAD), which this project depends on).  You can do this by running `git submodule update --init --recursive`.

<table>

  <tr>
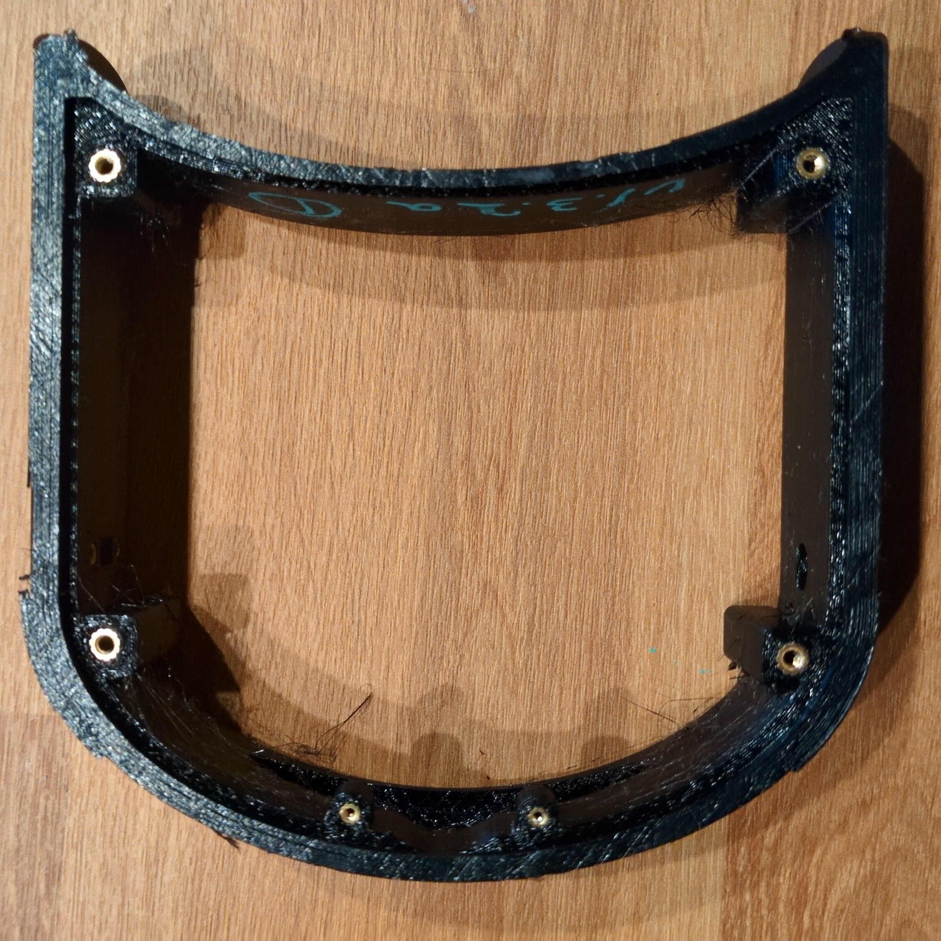
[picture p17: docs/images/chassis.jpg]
Picture of the bot's main chassis. It's in the shape of an outline of a cat's head
    <td style="width: 150px;"></td>
    <td>The <b>main chassis</b> is what holds the two lids together, and absorbs most of the battles' impacts.  It's designed to be printed in TPU, ideally at 100% infill</td>
  </tr>

  <tr>
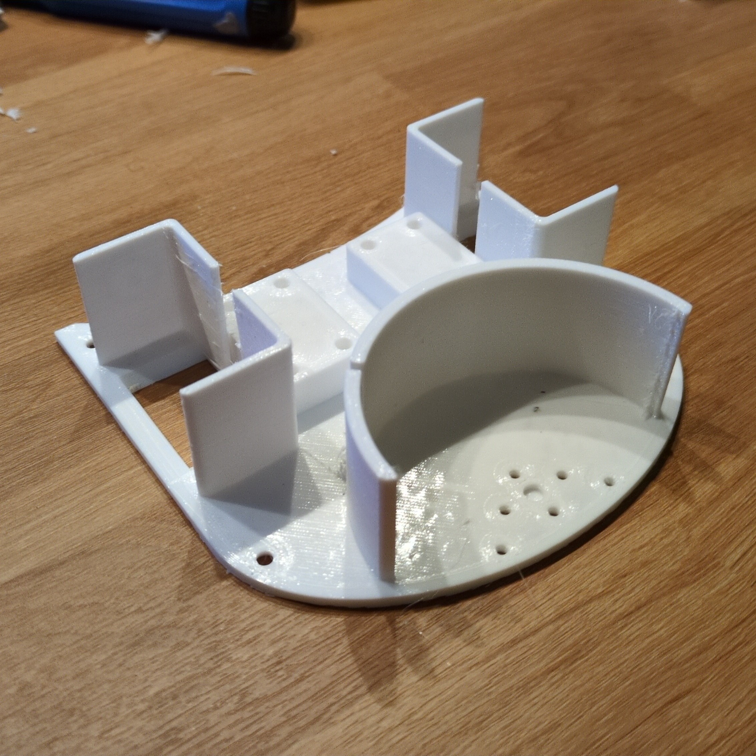
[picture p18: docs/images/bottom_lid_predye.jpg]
Picture of the bottom lid. It's in the shape of a cat's head but has lots of mounting parts attached to it
    <td style="width: 150px;"></td>
    <td>The <b>bottom lid</b> is what all of the internals of the bot are mounted onto.  Currently this should also be printed in TPU, but it's possible this will change in the future to something more rigid</td>
  </tr>

  <tr>
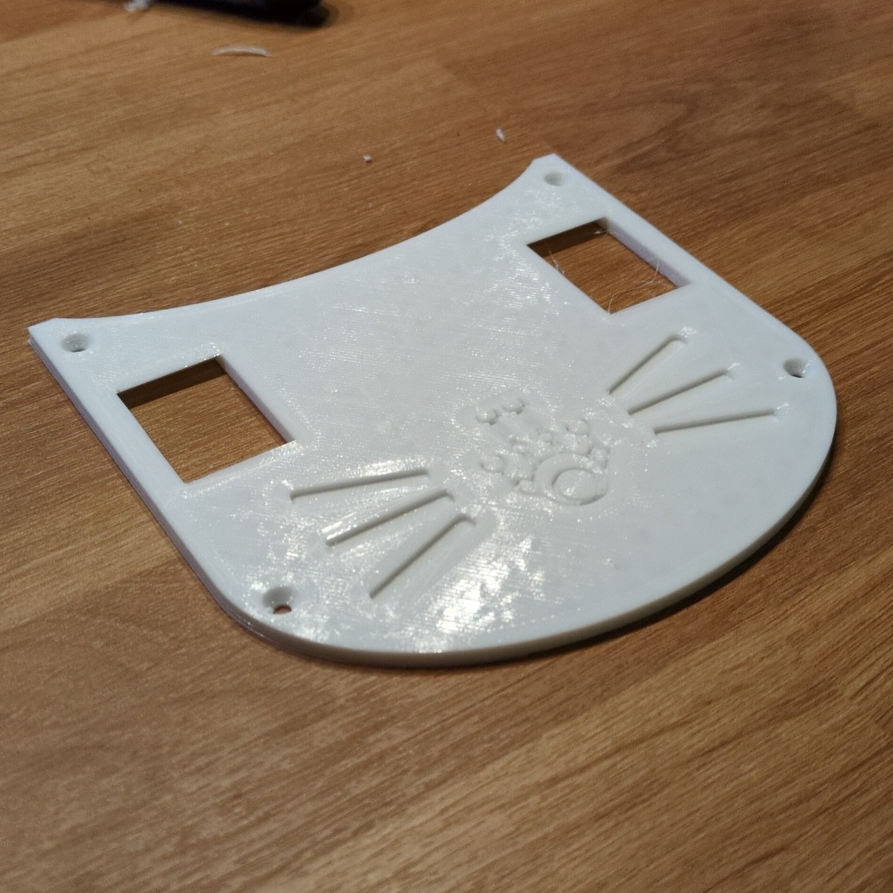
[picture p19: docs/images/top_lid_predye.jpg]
Picture of the top lid. It's in the shape of a cat's head and is flat
    <td style="width: 150px;"></td>
    <td>The <b>top lid</b> looks like the bottom lid but is flat on the inside.  This can be printed as one TPU piece, but...</td>
  </tr>

  <tr>
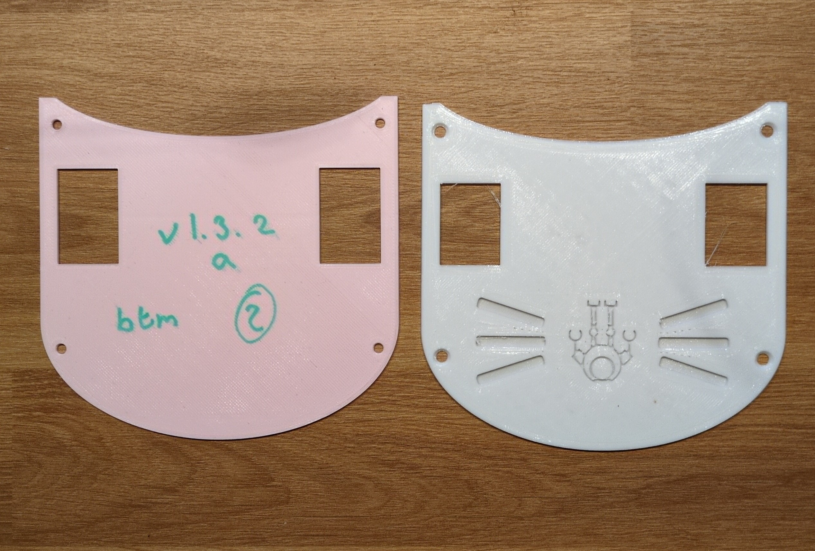
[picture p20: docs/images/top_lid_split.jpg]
Picture of the split top lid parts - two cat head shaped parts (one pink and one white) laid beside each other.
    <td style="width: 150px;"></td>
    <td>...I would recommend printing the <b>"split" lid</b> - this consists of a TPU top half and a PLA bottom half, which are glued together.  This helps to prevent lid bending when the contents are squished in.</td>
  </tr>

  <tr>
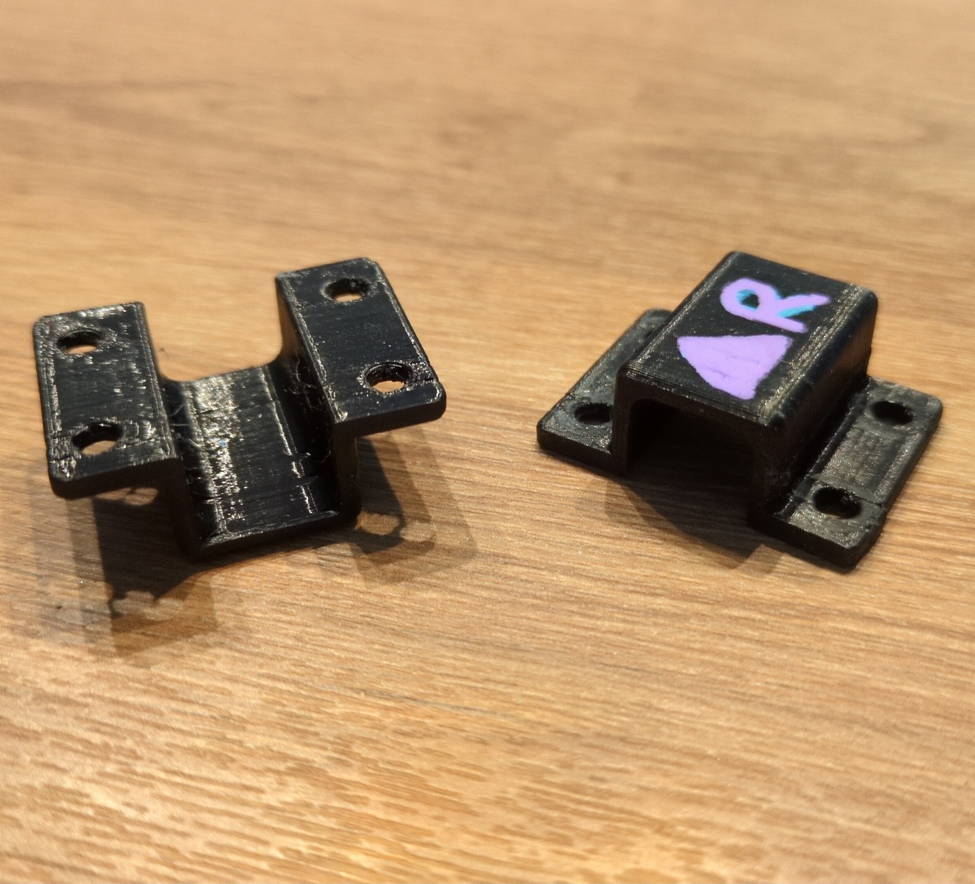
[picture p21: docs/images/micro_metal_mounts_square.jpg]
Two micro metal mounting brackets, with the left one upside down to show the inside
    <td style="width: 150px;"></td>
    <td>The two motors are held on to the bottom lid with <b>micro metal brackets</b>, usually printed in something solid like PLA or PETG</td>
  </tr>

  <tr>
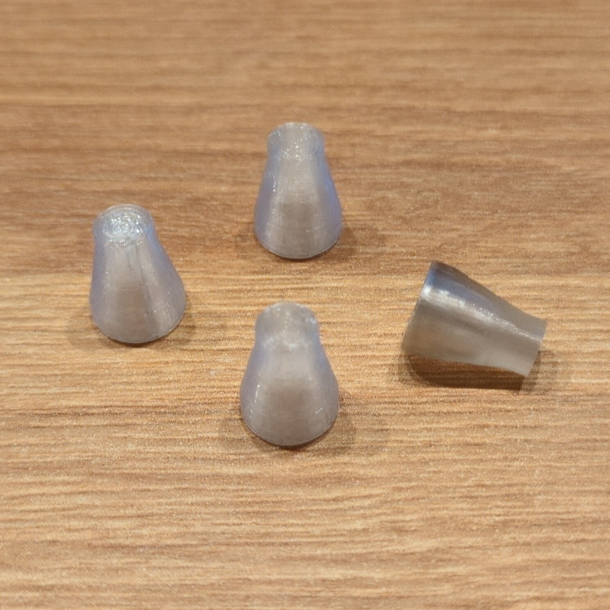
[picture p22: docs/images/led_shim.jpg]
Picture of four LED sims. They look like translucent cones
    <td style="width: 150px;"></td>
    <td><p>The bot's status LED is held into the chassis with a <b>LED shim</b>.  As well as securing the LED into the chassis, the shim provides a flat bit on the outside of the chassis so the LED doesn't need to poke through.  The light is diffused through the shim to the outside.</p>
    <p>I would print this out of translucent PLA, with 0% infill and a circular top/bottom infill pattern (to prevent the light from being too scattered).</p>
    </td>
  </tr>

</table>

> [!TIP]
> When printing the bottom lid, it's recommended that you print the area around the weapon mounting holes with 100% infill.
>
> When using Cura, you can create a support blocking cube, position and scale it around the mounting holes, then specify it to have 100% infill at overlapping areas in the Per-Model settings.
>
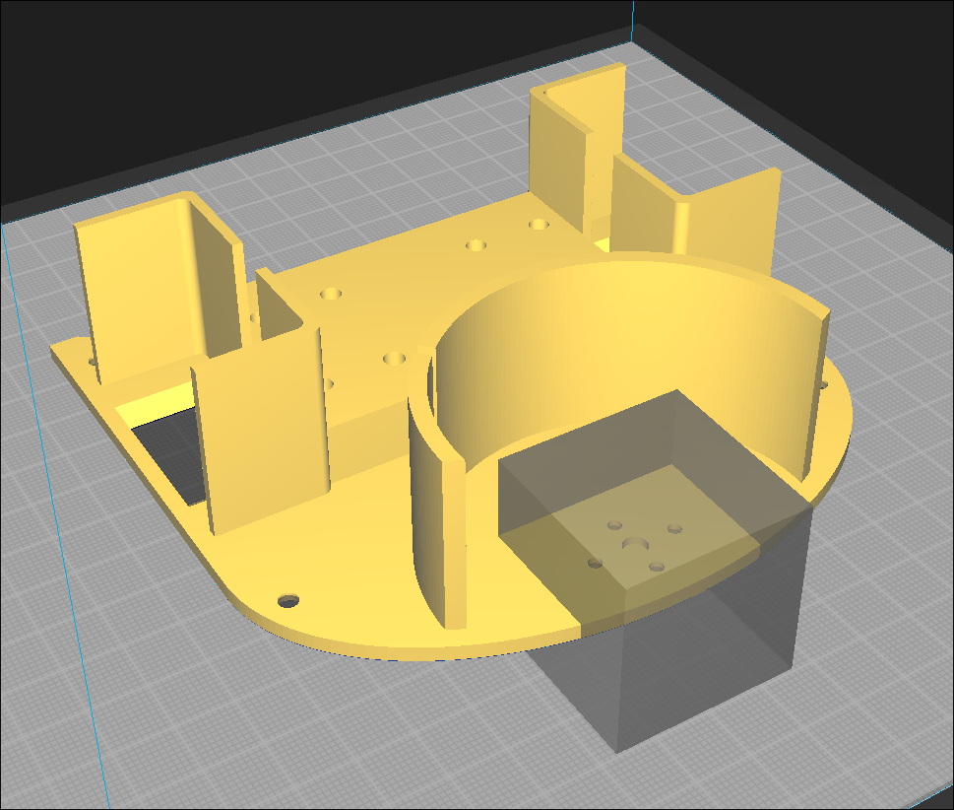
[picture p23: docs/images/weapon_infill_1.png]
Screenshot of cura showing lid_bottom.stl with a support blocker cube over the weapon mounting holes
> 
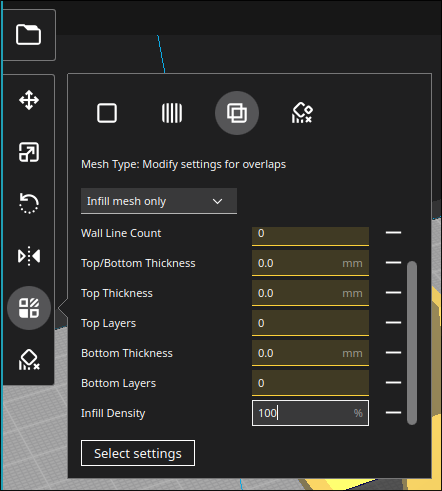
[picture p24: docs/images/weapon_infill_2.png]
Screenshot of cura's per-model settings menu showing the cube set to have 100% infill, with mesh type set to 'Modify settings for overlaps'
> 
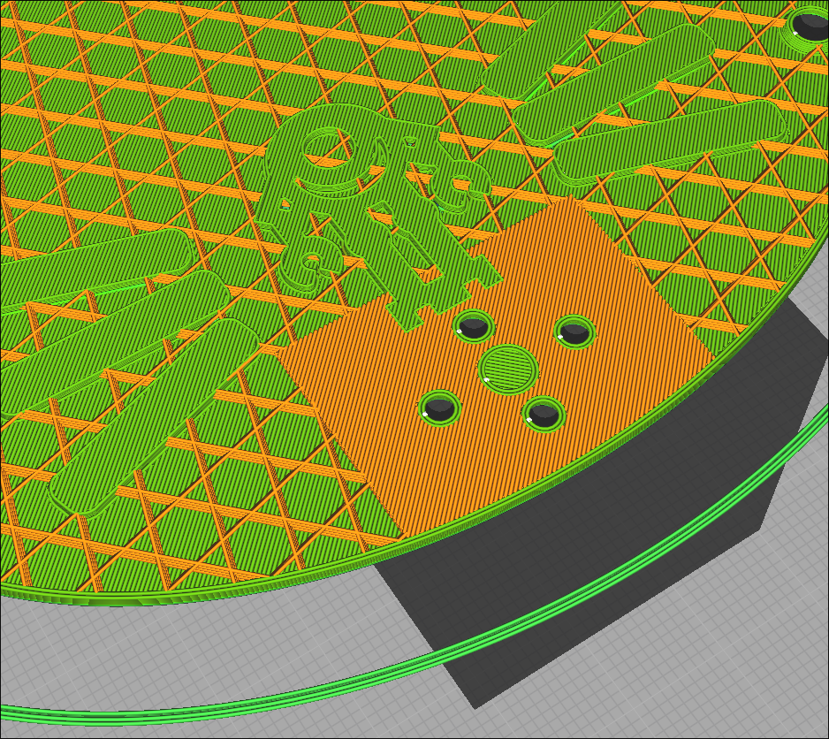
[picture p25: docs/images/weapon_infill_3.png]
Screenshot of the result of slicing, only showing up to the 8th layer; the area around the mounting holes is at 100% infill while the rest of the model is at 20% infill
> 

## Wheels
While you can use any 42mm diameter wheels, Cat Bot includes some funky custom wheels.  These have three parts:

<table>

  <tr>
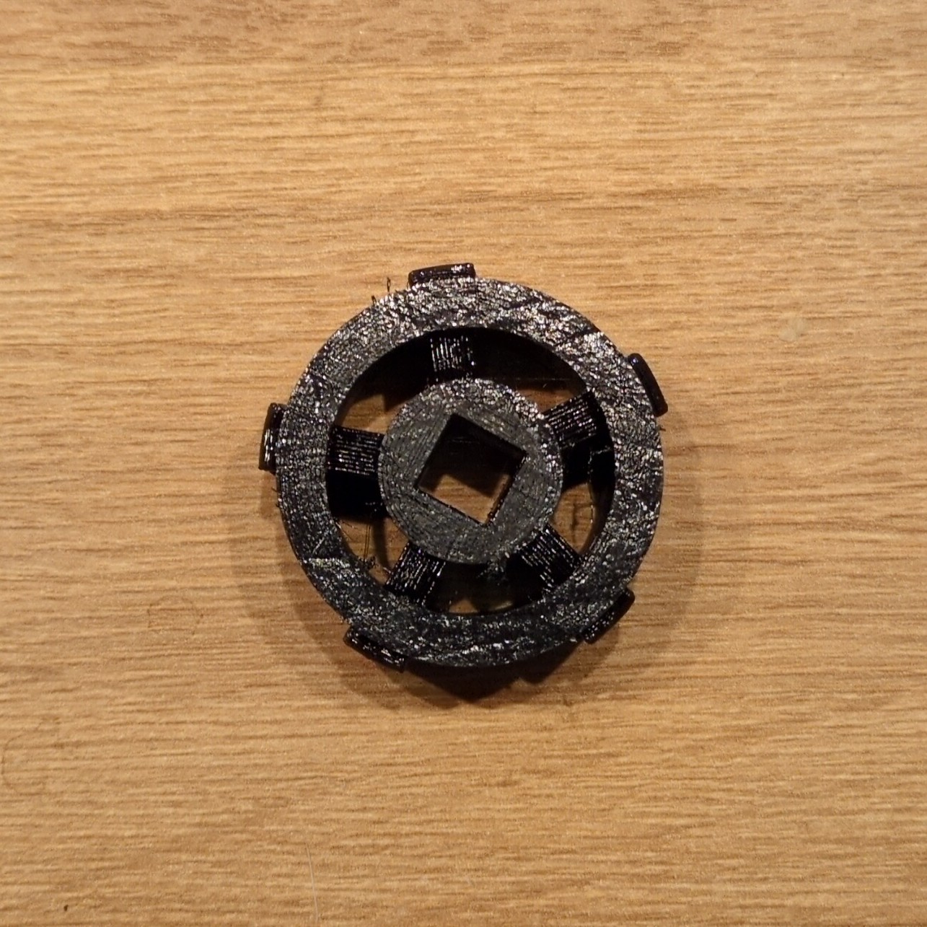
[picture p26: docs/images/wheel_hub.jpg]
Picture of a wheel hub. It's a black circular thing with five spokes and five 'lips' sticking out of the sides
    <td></td>
    <td>The main hub, printed in TPU at around 20% - 50% infill depending on how squishy you want it</td>
  </tr>

  <tr>
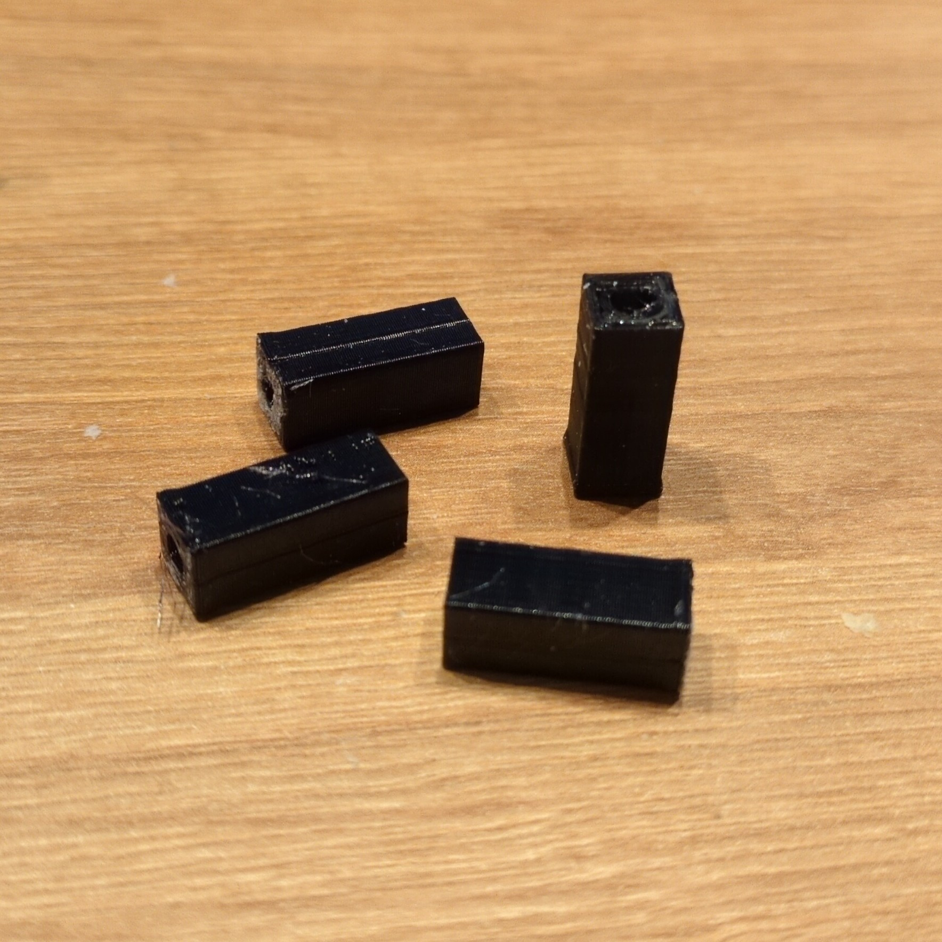
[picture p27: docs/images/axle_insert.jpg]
Picture of four axle inserts. They look like small but long rectangles with a D-shaped hole in the centre
    <td></td>
    <td>The axle insert, printed in something rigid like PETG</td>
  </tr>

  <tr>
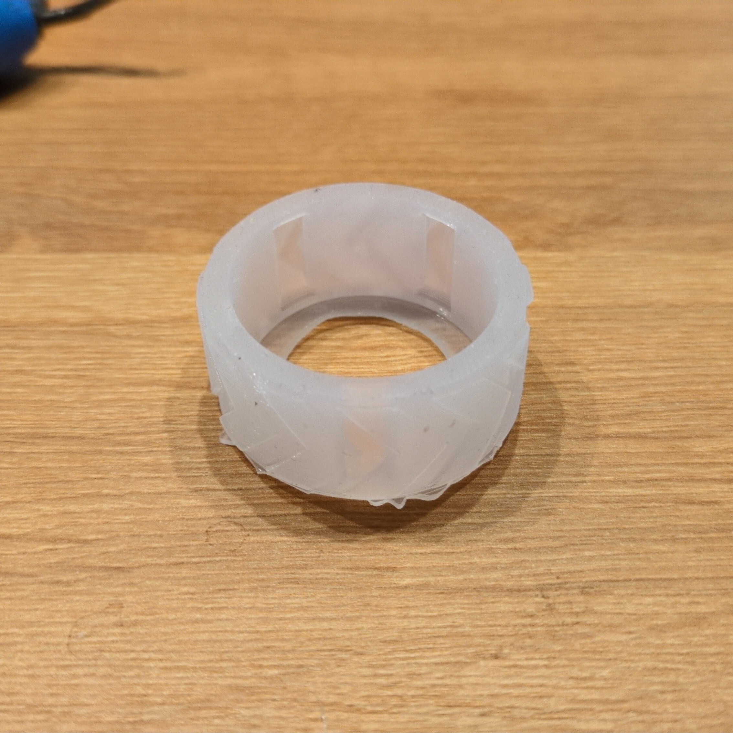
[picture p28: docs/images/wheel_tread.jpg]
Picture of the wheel tread. It's a hollow cylinder with chevrons on the outside
    <td></td>
    <td>The grippy tread of the wheel, cast from two-part silicone</td>
  </tr>

</table>

To assemble the wheel, push a hub insert into the square hole in the hub.  Pull the tyre onto the hub, and make sure to align the lips on the hub with the gaps on the inside of the tyres

<center>
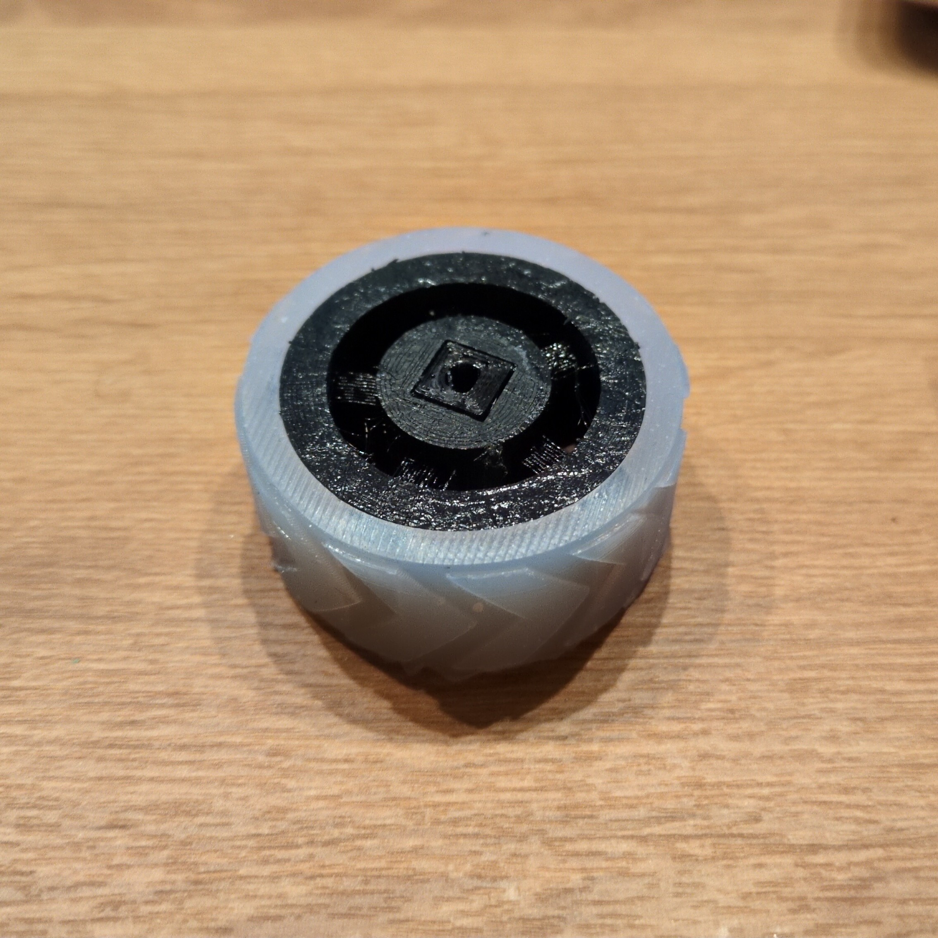
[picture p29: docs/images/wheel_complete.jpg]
Picture of the assembled wheel

</center>

> [!TIP]
> **Casting the tyres**
> 
> To make the mold for the tyres, I used Cura's Mold Mode.  Load the original tyre STL into Cura, then search for Mold Mode in the slicer settings and enable it.
>
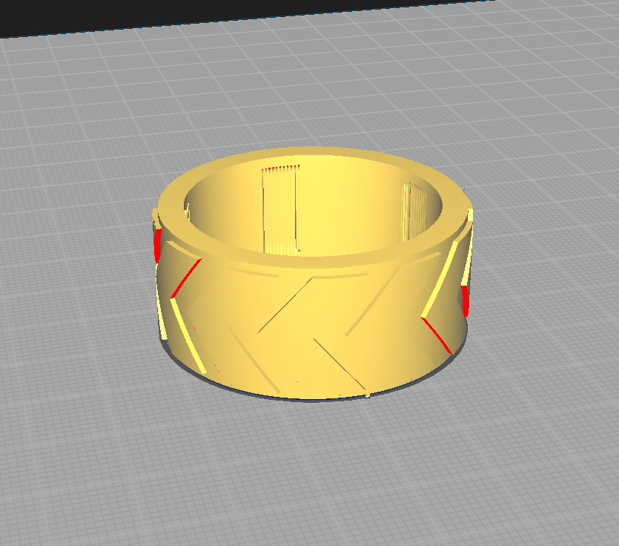
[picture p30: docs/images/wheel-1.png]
A screenshot showing the tyre model loaded into Cura
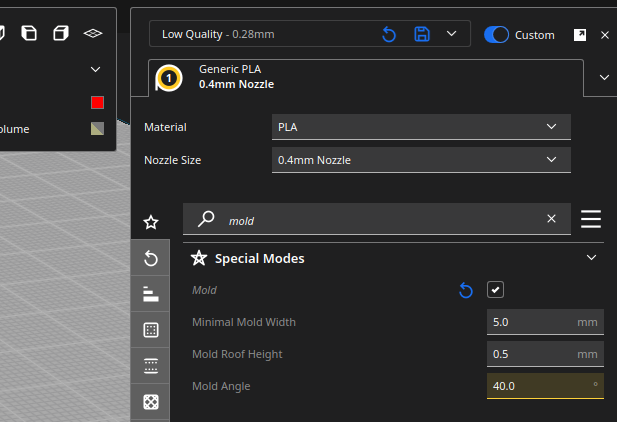
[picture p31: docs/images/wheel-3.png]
A screenshot showing Cura's mold mode setting
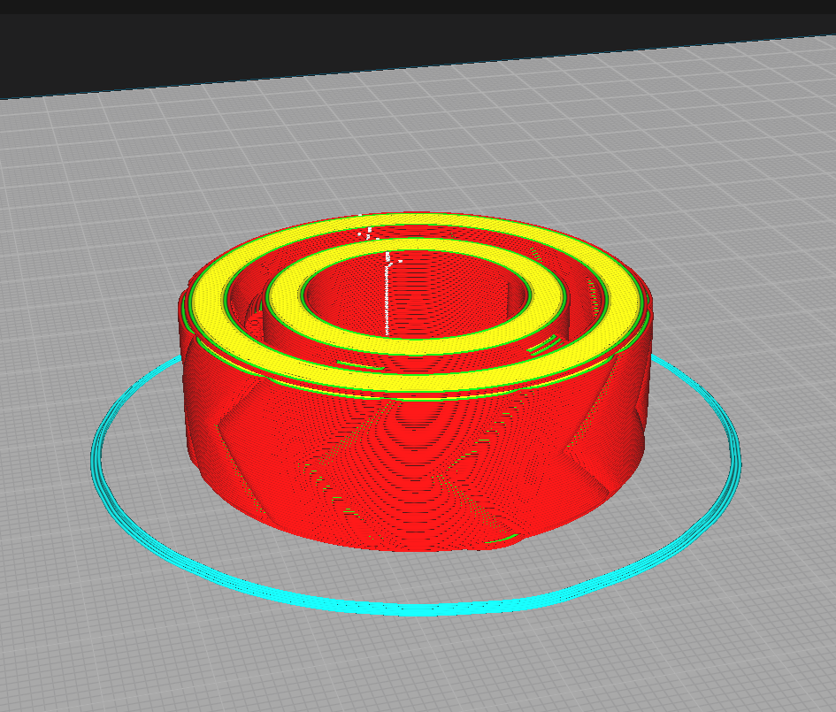
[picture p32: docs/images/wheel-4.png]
A screenshot showing the model now being sliced as mold
> 
> 
> This should make a mold, but there won't be a bottom.  To solve this, select the model and go to the translate (move) menu.  Untick "Drop Down Model", and set the Z offset to 5mm.  This should raise the model up, creating a base for the mold.
> 
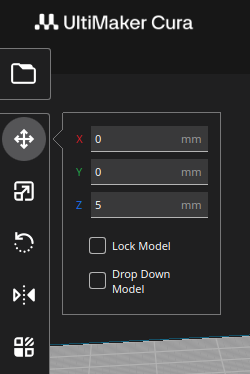
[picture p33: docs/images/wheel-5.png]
A screenshot showing Cura's model translation settings
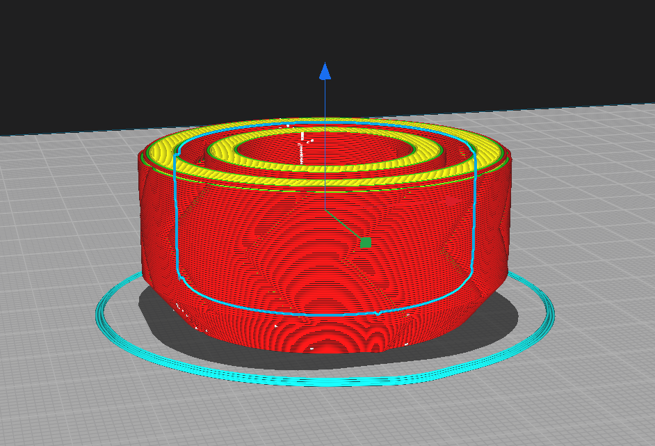
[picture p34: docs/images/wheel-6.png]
A screenshot showing the model now rendering as a mold with a bottom
> 
> 
> After printing the mold, mix your silicone (I found I needed about 15g per wheel) and pour it slowly in.  Since the mold is a big circle, I tried to move the pour around its circumference to ensure it was even.  I found that over the first few hours after pouring, the silicone level would fall, so you might need to top it up after a bit.
> 
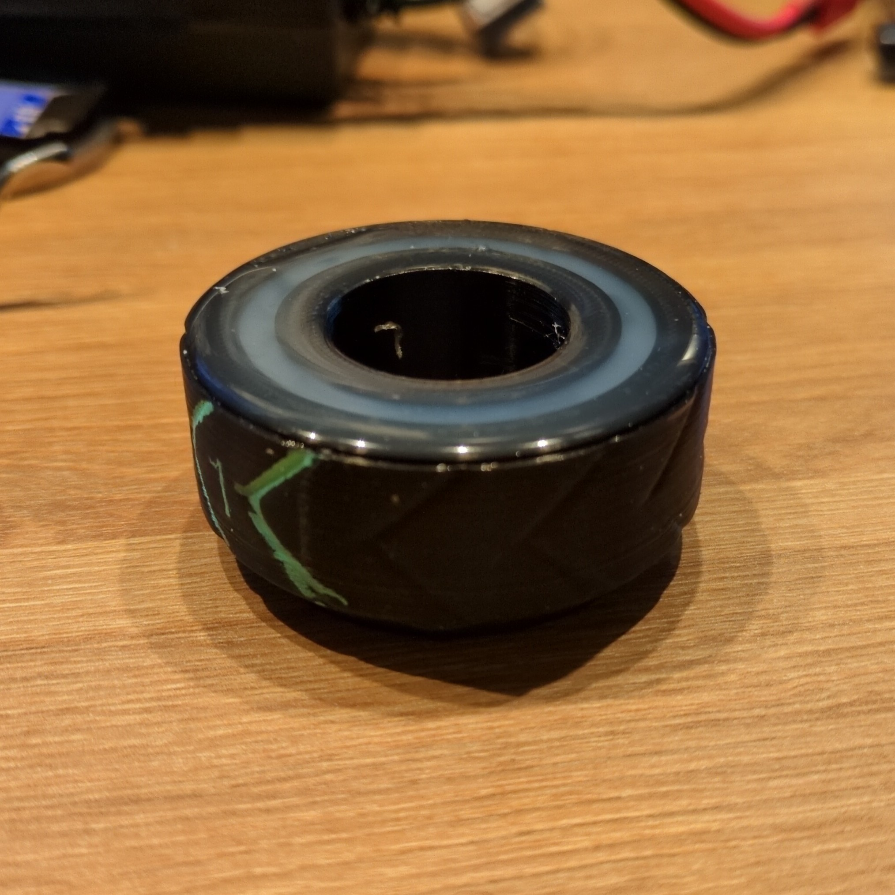
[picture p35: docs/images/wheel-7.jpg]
A picture of the tyre mold full of silicone
> 
>
> Once the silicone has cured, removing the tyre can be a bit tricky.  If you're careful, you can pry it out using a flat thing like a flathead screwdriver and a pair of flat tweezers.

## Colours
The colours of everything are up to you but generally I print the chassis and wheels in black, the top lid in pink, and the bottom lid in blue.  

It's kinda hard to get pink and light blue TPU, so generally I print them in white and dye them using **synthetic** clothes dye (eg: Rit) (non-synthetic dye doesn't seem to work that well).  The process I found worked was:

- pour half a bottle of dye into medium sized tub (around 3 litres ish) full of water.  
- place the part into the dye water and use a wooden block to hold the part under the water, making sure the block was only touching internal surfaces since they would end up discoloured.
- leave the part for about an hour, and maybe give it an extra 30 mins if it looked like it needed it.

<center>
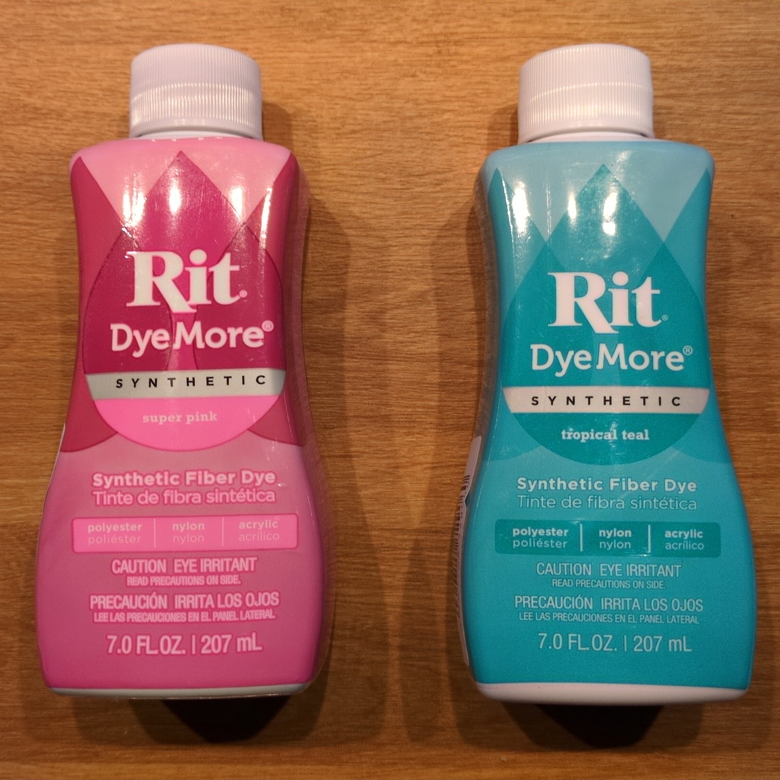
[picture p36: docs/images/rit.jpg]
A picture of two bottles of synthetic clothes dye - one pink and one blue

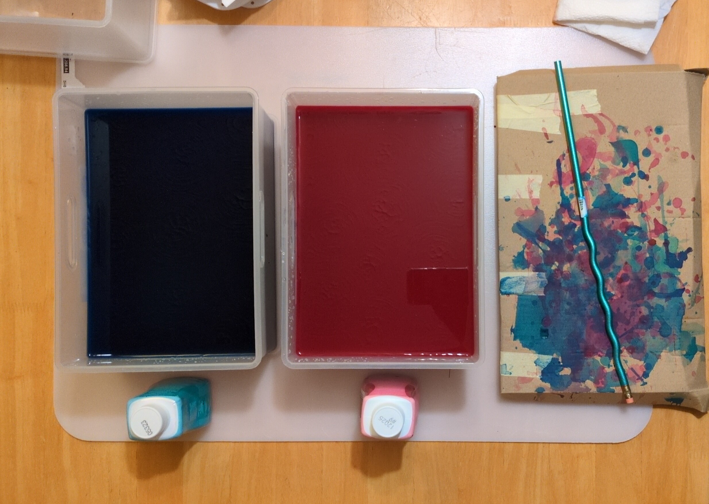
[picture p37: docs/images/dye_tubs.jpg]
A picture of two tubs full of dye dissolved in water, along with a drying mat, all placed on a large plastic mat

</center>

## Next Part
With everything printed, molded, and dyed, you're ready to move onto the next part!

<center>
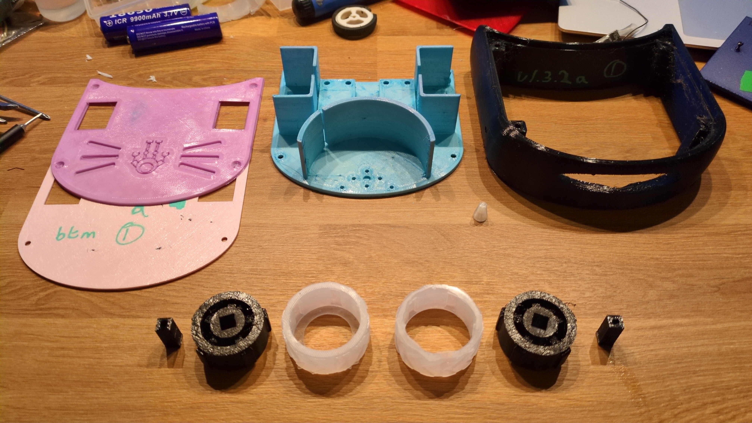
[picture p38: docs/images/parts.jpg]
A picture of all the finished parts of the bot laid out on a desk

</center>

# Wiring
Within the hobby of combat robotics there are many different ways to wire a cat.  While Cat Bot is designed around a few specific design choices (eg: motor type), most of the wiring is really up to you!  

This section of the document describes the wiring that I used for the electronics, but it's more of a guide than a ruleset.  Feel free to deviate from or ignore this section completely!  (Just make sure your wiring can handle the amount of power your bot is expected to draw, and has the appropriate failsafes!)

<center>
Diagram showing the wiring of the bot's electronics
</center>

In general there are a few main components.  Please refer to the BOM for info on specific component choices, but broadly there should be:

- the **battery** supplies power to everything.  I used a 2 cell, 300mAh LiPo battery, but I would have gone with a 3 cell if there was more space inside the bot.  Make sure your battery can source enough current for all the other components to use.
- the **power switch** is recommended since you can cut the power in an emergency without having to undo all the lid screws
- the **drive ESC** supplies power and drives the two main brushed drive motors.  You could use two ESCs (one for each motor) but dual ESCs are a lot more convenient
- the **weapon ESC** drives the brushless spinner weapon motor
- the **receiver** receives input from a remote controller.  Most bots use a RX module that supports a standard flight controller, but in my case I used an ESP32 with some [custom firmware](https://github.com/atctwo/bbrx) for use with a Bluetooth gamepad
- a **power led** to show when the bot is running
  - generally this can be put across the battery power with an appropriate resistor, but in my Cat Bot build the power LED is [controlled by the ESP32](https://github.com/atctwo/bbrx/blob/main/docs/usage/status_led.md) to show controller connection status

# Assembly
Now that you have everything printed and wired, you can start to assemble the bot!  Make sure you have a screwdriver and a way to insert brass inserts.

## Bottom Lid
The base of the bot is the bottom lid - this is the part onto which all the motors and electronics are mounted.  In between the wheel walls, there are two blocks each with four holes - these are for M3 brass inserts.  Both motors are held in place by a [micro metal bracket](../renders/wheels/micro_metal_bracket_v2.stl), which screw into place using four pan-head M3 screws each.  

<center>
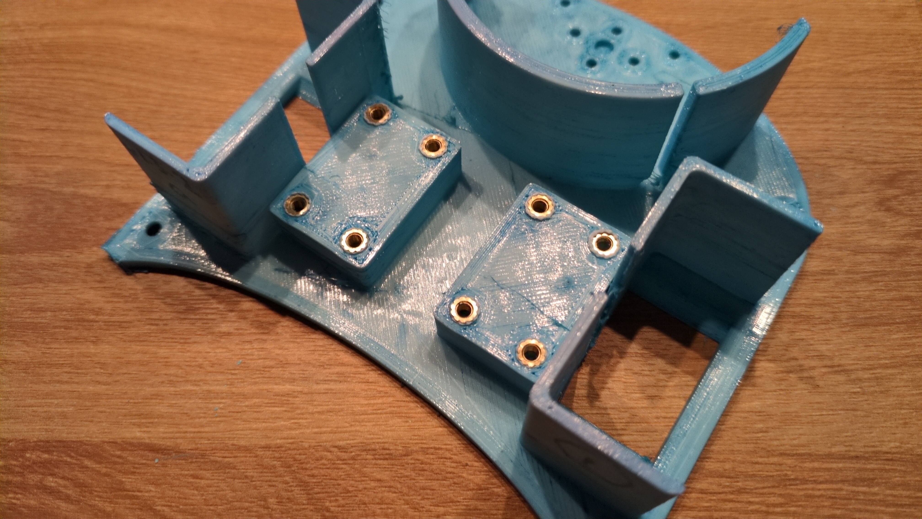
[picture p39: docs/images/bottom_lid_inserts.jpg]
A picture of the bottom lid with brass inserts inserted into the motor mount holes

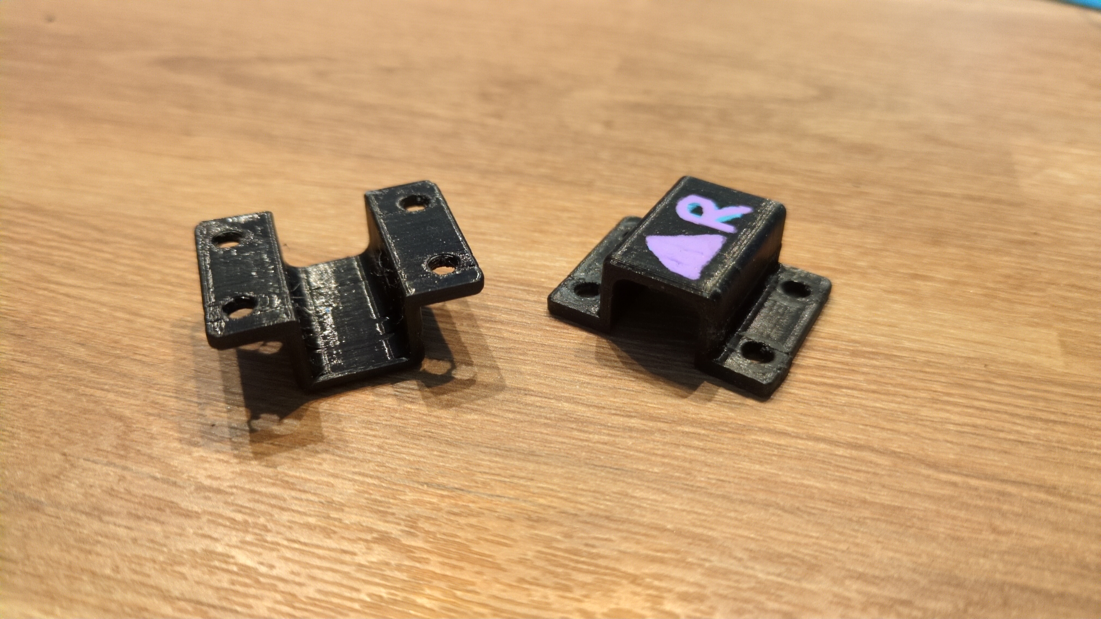
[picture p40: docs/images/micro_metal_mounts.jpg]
Two micro metal mounting brackets, with the left one upside down to show the inside

</center>

At this point, attach the wheels to the motors, and mount the motors to the bottom lid using the brackets.  It's a good idea to attach the wheels to the motor axles before attaching them to the bottom lid, since it's quite difficult to add or remove the wheels once the motors are mounted.

<center>
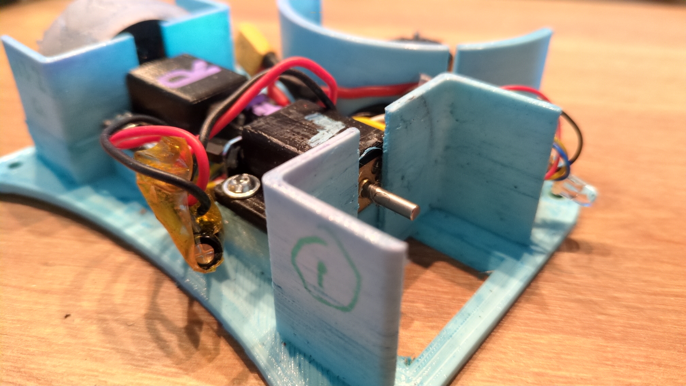
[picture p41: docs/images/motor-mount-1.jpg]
A picture the left drive motor mounted into the chassis, with the axle sticking out into the walled-off area for wheels

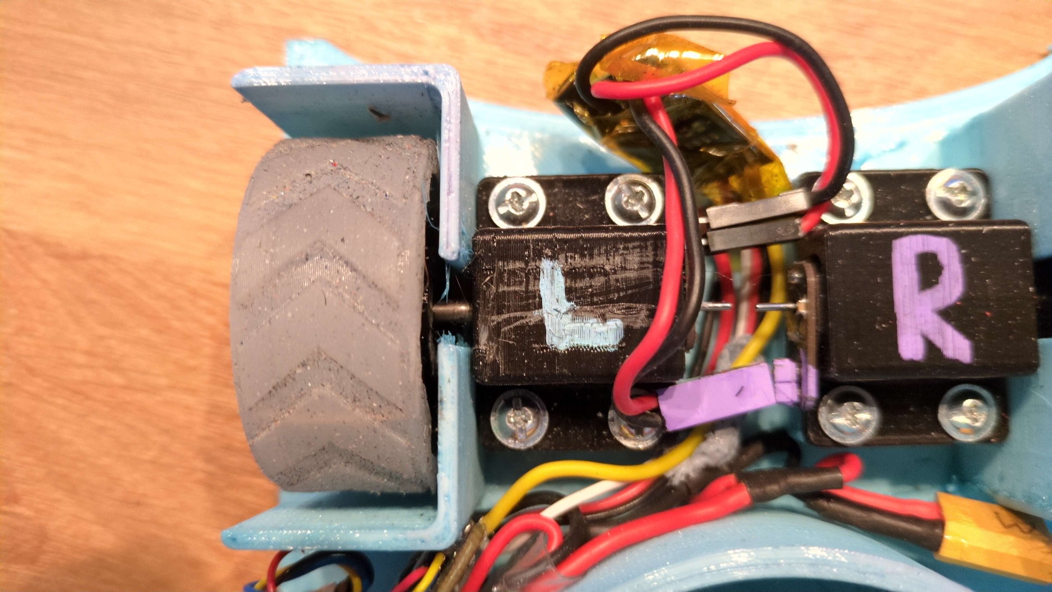
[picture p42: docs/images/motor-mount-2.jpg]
A top down view of the motor and wheel mounted into the chassis

</center>

The weapon motor mounts onto the front of the bottom lid.  There are four countersunk holes for M2 screws to go through the lid into the motor.  Make sure to put a bit of threadlock on them to mitigate the effects of vibration.

There are an additional two holes around the motor - these are to secure the edge of the lid to the chassis, so we'll look at these later.  The wires of the motor can be kept out of the way by slotting them into the slot in the protective wall around the spinner area.  

<center>
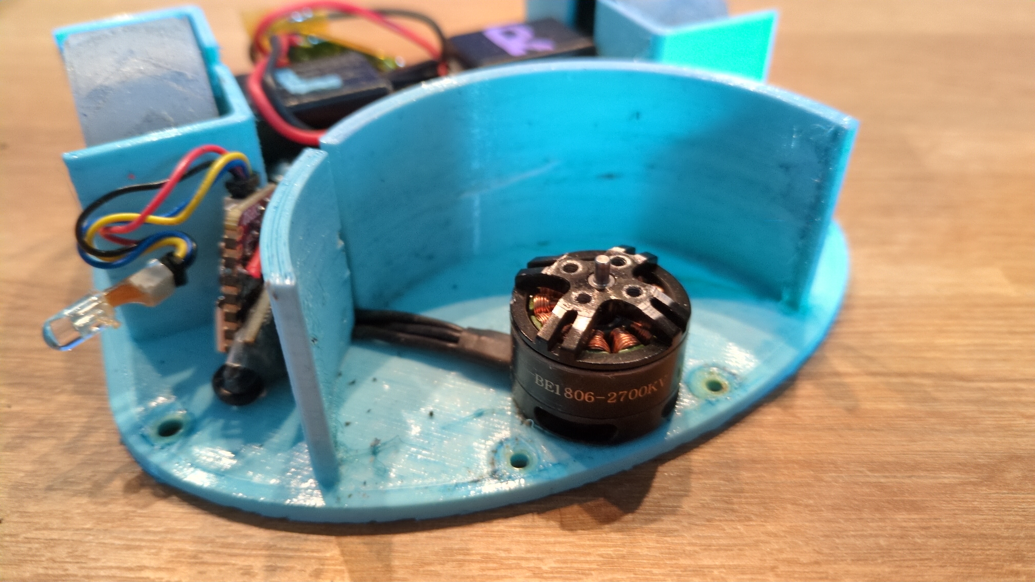
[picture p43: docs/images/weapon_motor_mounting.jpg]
A picture showing the weapon motor mounted onto the front of the bottom lid, with its wires routed through a small hole in the protective wall

</center>
<center>
A picture showing the screws around the bottom of the weapon motor, and what they are used for
</center>

Don't attach the weapon blade yet, since it's easier to install once the main chassis is installed.

## Chassis and Weapon
I would install the power switch into the chassis at this point because it can be tricky to do later.  Press the two M2.5 brass inserts into the holes around the switch hole in the main chassis.  The switch will probably end up quite recessed, so I would colour the top of the actuator with a little bit of paint so you can see it.  You may also need to use a flathead screwdriver to actuate the switch once it's installed.

<center>
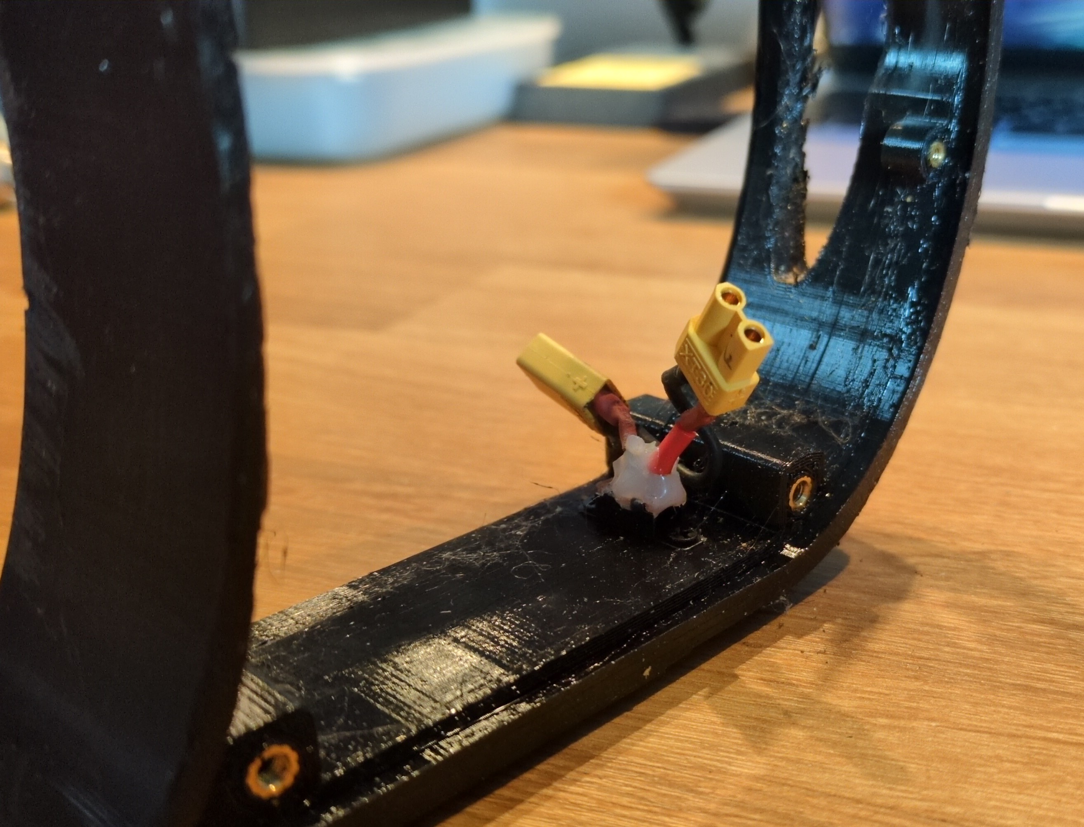
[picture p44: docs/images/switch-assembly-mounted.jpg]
A picture of the power switch assembly mounted into the chassis

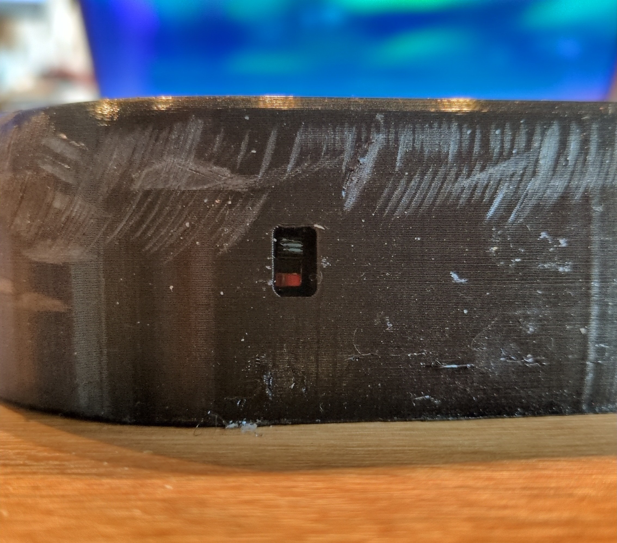
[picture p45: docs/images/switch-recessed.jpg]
A side-on view of the switch from the outside of the chassis, showing the blue painted top of the switch actuator

</center>

In theory, you could run the whole bot with just the bottom lid, but then your electronics would be exposed.  As such, the bottom lid attaches to the main chassis via four M3 screws, into four M3 brass inserts in the chassis corners.  Make sure you get the chassis the right way up, since the spinner blade has to protrude from the hole in the front.  

<center>
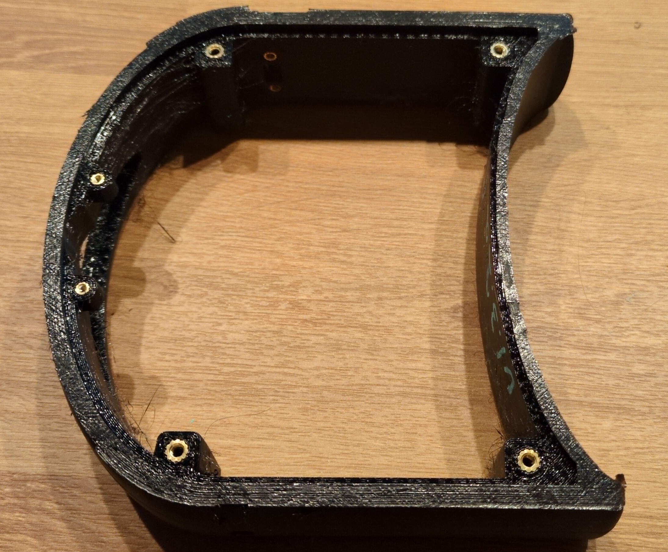
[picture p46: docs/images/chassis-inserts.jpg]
A picture of the chassis with brass inserts inserted into the corners and switch hole

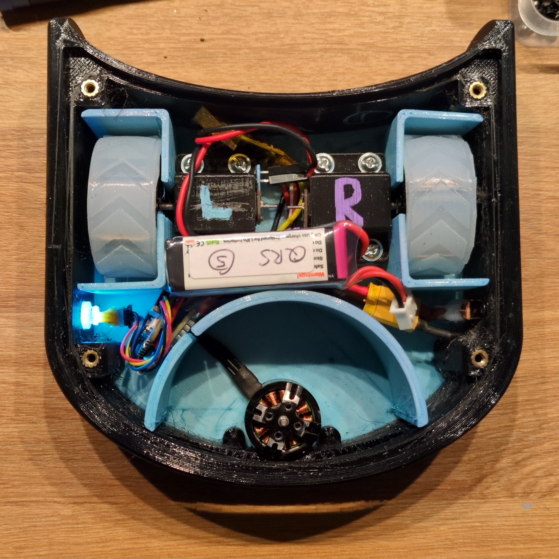
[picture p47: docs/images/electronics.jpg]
A picture of the bot with the top lid removed, with all the electronics tightly packed in

</center>

When the bottom lid is printed from TPU, the forces produced by the spinner can cause the whole weapon assembly to "wobble".  This can lead to the weapon damaging the opening in the chassis, and possibly reducing the overall force of the weapon.  That's why there are two extra M2 holes around the motor!  These allow the edge of the bottom lid to be fastened onto two M2x3 inserts in the "nubs" protruding from the inside of the chassis. 

<center>
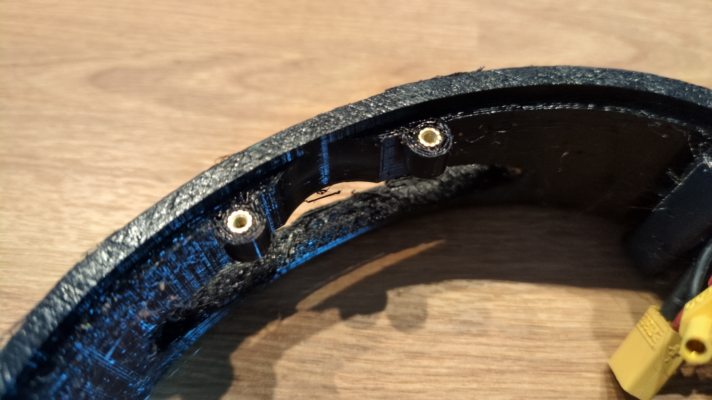
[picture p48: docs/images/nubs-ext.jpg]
The nubs as viewed from below, showing the brass inserts

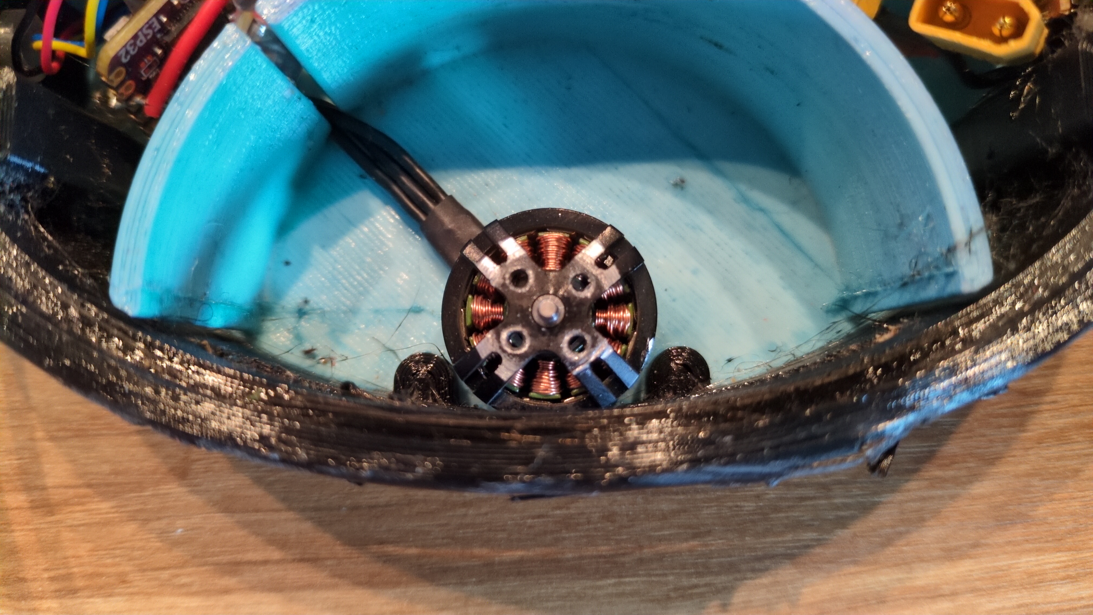
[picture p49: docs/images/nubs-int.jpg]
The nubs as viewed from inside the chassis with the bottom lid attached, with the weapon motor sitting between them

</center>

Speaking of the spinner, the blade can be attached to the spinner motor by sliding it in through the hole in the front of the bot, and fastening with four M2 screws.  These screws should ideally have a large / thick head to be able to handle the forces put on them by the weapon.  I would also apply some (lots of?) threadlock since these screws will very quickly vibrate out.

<center>
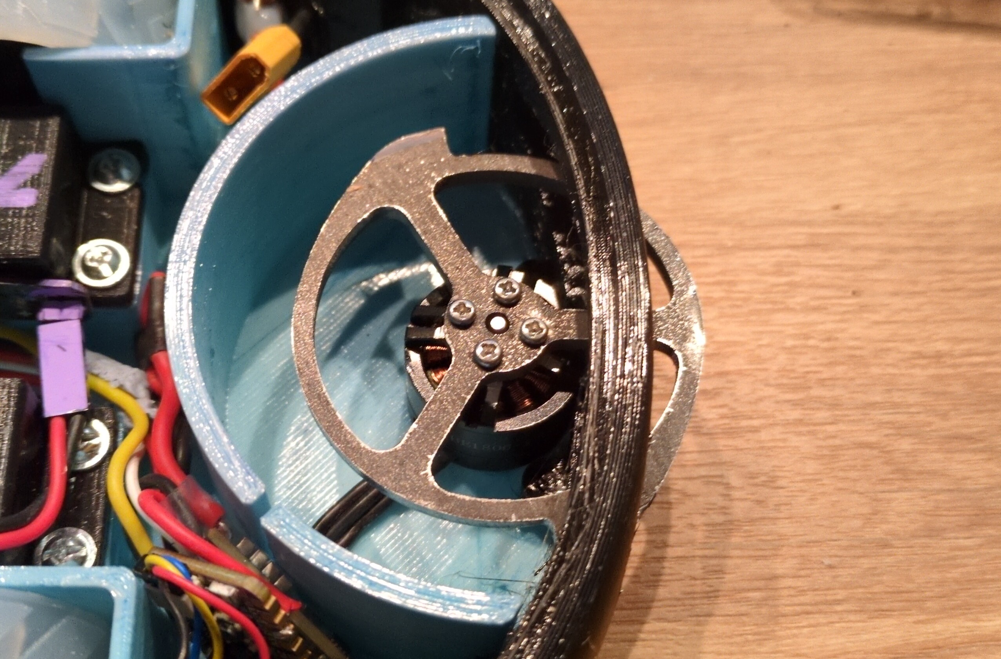
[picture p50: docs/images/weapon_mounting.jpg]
A picture of the weapon mounted onto the weapon motor

</center>

For the status LED, a 5mm LED should friction fit into the shim, which should friction fit into the hole on the side of the chassis.  If either interfaces are a bit loose, but a wee bit of super glue on when inserting.

<center>
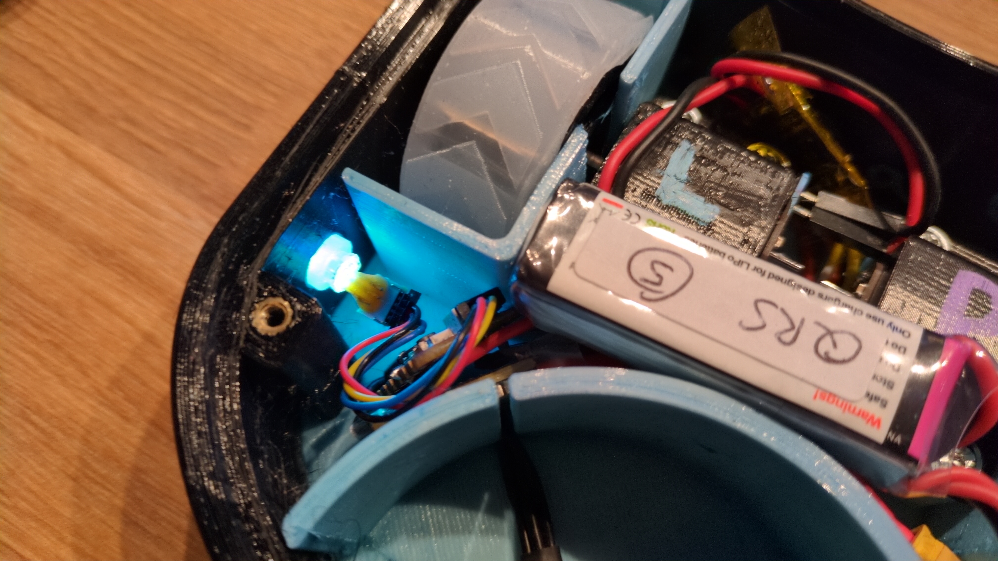
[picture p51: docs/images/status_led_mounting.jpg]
A closeup of the status LED mounted to the chassis via the shim

</center>

Finally, the top lid can be attached to the main chassis in the same way the bottom lid was.

<center>
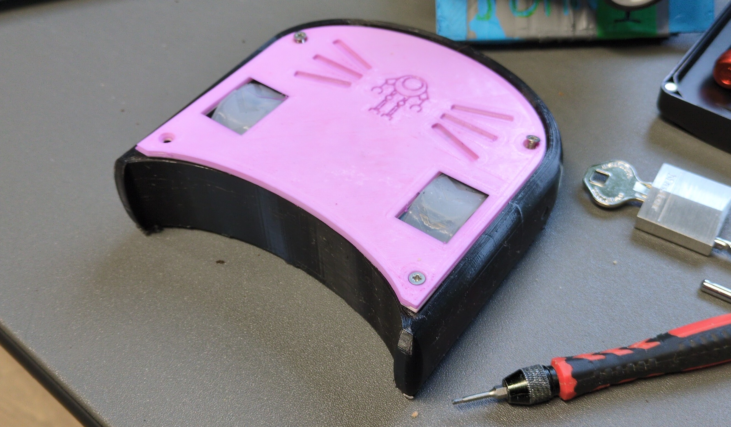
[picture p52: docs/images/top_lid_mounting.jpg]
A picture of the bot with the top lid attached to the chassis

</center>

That's it!  Connect a battery, flip the switch, pair your controller, and have fun :3

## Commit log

2024-08-24 initial commit :)
    [1806.step, N20 v2.step, N20 v2.stl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]
2024-08-24 space out wheels a bit more
    [cat_bot.scad]
2024-08-29 added gap for other interior features
    [cat_bot.scad]
2024-08-29 updated bom
2024-08-29 big cat v1.0.1 moved gearbox back a bit, made lid screw holes a bit bigger
    [lid_bottom.stl, lid_top.stl, main_chassis.stl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]
2024-08-29 little cat v1.0.0
    [cat_bot.scad, lid_bottom.stl, lid_top.stl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]
2024-08-30 update flange size on motor bracket
    [cat_bot.scad, micro_metal_bracket.scad, micro_metal_bracket.stl]
2024-09-14 little cat v1.0.1
    [lid_bottom.stl, lid_top.stl, main_chassis.stl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]
2024-09-14 little cat v1.0.2
    [cat_bot.scad, tpu_shielding_hole.stl, tpu_shielding_no_hole.stl]
2024-09-25 little cat v1.0.3
    [cat_bot.scad, tpu_shielding.stl]
2025-05-08 made mouth hole round
    [cat_bot.scad]
2025-05-08 remove body size dependency on tpu size
    [cat_bot.scad]
2025-05-08 slight parameter tuning
    [cat_bot.scad]
2025-05-11 make mouth a little taller
    [cat_bot.scad]
2025-05-11 tpu gap
    [cat_bot.scad]
2025-05-11 add padding for motor in main chassis
    [cat_bot.scad]
2025-05-12 screw holes for weapon motor
    [cat_bot.scad]
2025-05-12 added power switch
    [cat_bot.scad, switch.stl]
2025-05-12 tuned things to make it a bit lighter
    [cat_bot.scad]
2025-05-12 big hole !
    [cat_bot.scad]
2025-05-12 little hole ! for cable managing the weapon motor wires
    [cat_bot.scad]
2025-05-12 whoops forgor to unhlghlight stuff
    [cat_bot.scad]
2025-05-12 tweaks to the wheel assembly
    [cat_bot.scad]
2025-05-15 extend switch hole through tpu
    [cat_bot.scad]
2025-07-02 add tpu switch toggle
    [cat_bot.scad]
2025-07-02 tpu shielding curved sides
    [cat_bot.scad]
2025-07-02 weapon screws are now countersunk
    [cat_bot.scad]
2025-07-02 update year
    [cat_bot.scad, lid_bottom_v1.1.0a.stl, lid_bottom_v1.1.0b.stl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]
2025-07-02 update bom
2025-07-04 round sides on the main chassis
    [cat_bot.scad]
2025-07-04 shorten weapon mounting block
    [cat_bot.scad]
2025-07-04 added missing curved bit
    [cat_bot.scad]
2025-07-05 made bot a little shorter
    [cat_bot.scad]
2025-07-05 move lipo
    [cat_bot.scad]
2025-07-05 tune animation offsets
    [cat_bot.scad]
2025-07-05 adjust tpu shielding sides
    [cat_bot.scad]
2025-07-05 lipo animation
    [cat_bot.scad]
2025-07-05 move switch mounting holes a bit
    [cat_bot.scad]
2025-07-05 more switch hole stuff
    [cat_bot.scad]
2025-07-18 increase lid thickness (for tpu)
    [cat_bot.scad]
2025-07-18 added tpu wheel
    [cat_wheel.scad]
2025-07-18 v1.2.0 renders
    [bottom_lid_v1.2.0a.stl, bottom_lid_v1.2.0b.stl, cat_wheel_36mm.stl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]
2025-07-18 weapon stabiliser mounts
    [cat_bot.scad]
2025-08-20 make lid brass insert holes smaller
    [cat_bot.scad]
2025-08-20 improved motor bracket
    [micro_metal_bracket.scad]
2025-08-20 updated motor mount to work with v2 of the motor bracket. and also the mounting block was split into two blocks
    [cat_bot.scad]
2025-08-20 make weapon hole a bit wider
    [cat_bot.scad]
2025-09-29 remove debugging
    [cat_bot.scad]
2025-09-29 wheel separation
    [cat_bot.scad]
2025-09-29 v1.3 renders
    [bottom_lid_v1.3.0a.stl, main_chassis_v1.3.0a.stl, top_lid_v1.3.0a.stl]
2025-09-29 funky new wheels :3
    [cat_wheel.scad, cat_wheel_36mm.stl, cat_wheel_42mm.stl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]
2025-09-29 update bom for v1.3.1
2025-09-29 clean up repo and update readme
    [cat_bot.scad, cat_wheel.scad, micro_metal_bracket.scad]
2025-09-29 add custom wheel and switch mounts to BOM
2025-10-21 update import paths
    [cat_bot.scad]
2025-10-22 added tyre feature to wheel
    [cat_wheel.scad]
2025-10-23 added chevrons to wheels
    [cat_wheel.scad]
2025-11-19 update weapon mounting screw length
2025-11-19 wheel tuning
    [cat_wheel.scad, cat_wheel_v3.0_insert.stl]
2025-11-19 fix import path
    [cat_bot.scad]
2025-11-19 fix import path 2
    [cat_bot.scad]
2025-11-19 experimental cat ears :3
    [cat_bot.scad]
2025-11-19 add led shim
    [cat_bot.scad, cat_led_shim.scad, cat_led_shim.stl]
2025-12-02 v1.3.2 renders
    [bottom_lid_v1.3.2a.stl, main_chassis_v1.3.2a.stl, top_lid_v1.3.2a.stl]
2026-02-06 add split top lidd
    [cat_bot.scad]
2026-02-06 v1.3.2 split lid renders
    [top_lid_bottom_v1.3.2a.stl, top_lid_top_v1.3.2a.stl]
2026-02-08 update building.md - wiring and assembly
2026-04-09 added tyre guards to wheels
    [cat_wheel.scad]
